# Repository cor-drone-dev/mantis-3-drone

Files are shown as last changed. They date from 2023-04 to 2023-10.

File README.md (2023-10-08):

# mantis-3-drone

Mantis-3 installation instructions

Based on the Chinese guidebook by Clarence Chen

[User Manual](./user_manual.md)

## Installation

1. [Drone Body](./drone_body.md)

2. [Autopilot](./autopilot.md)

3. [Onboard Equipments](./onboard_equipments.md)

4. [Flight Tests](./flight_tests.md)

## Configurations

[MAVROS](./mavros.md)

### Multi-Robot Configurations

[Multi-Drone via MAVROS](./mavros_multi_drones.md)

## Tracking Control

[px4ctrl](./px4_ctrl.md)

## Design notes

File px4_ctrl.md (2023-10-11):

# Tutorial for PX4CTRL

The node name for the PX4 Controller is PX4CTRL.
It takes Odometry and the aircraft's IMU as feedback, receives desired position and attitude control commands, and provides precise control of the aircraft.

## Brief Introduction to the Controller

While the framework of this PX4CTRL controller is similar to the DJI N3 controller, the internal state machine and control algorithms have been completely rewritten to achieve higher stability and control accuracy.
The controller has three modes:

- **Manual Mode**: The terminal prints in green "MANUAL_CTRL(L1)". At this time, the controller does not function, and the flight control is entirely controlled by the remote control.
- **Fixed Point Mode**: The terminal prints in green "AUTO_HOVER(L2)". The controller will take over flight control through code, and the flight control will be in the "OFFBOARD" mode.
  The controller uses odometry feedback for fixed-point control. At this time, if you toggle the direction and throttle joysticks, the aircraft will move slowly, similar to flying in DJI Mavic's fixed-point mode.
  It will not receive the commands you send.
- **Command Control Mode**: The terminal prints in green "CMD_CTRL(L3)". At this time, the controller can execute the flight commands you send to it.
  This mode requires you to be in fixed-point mode, toggle the 6-channel joystick, and then send the control command to start, to ensure a thorough safety check.

### Coordinate System Definition

Odometry's pose is defined as forward x, left y, and up z. The aircraft's head points in the positive direction of the x-axis, and the throttle pull direction is the positive direction of the z-axis. It must be strictly aligned!
The speed definition of Odometry is slightly different from the official ROS. It's essential to note this. The official ROS defines speed under the body system, but most open-source VIOs define speed in the relative world system.
By default, PX4CTRL is also defined in the world system. If the speed you use is defined under the body system, change the `#define VEL_IN_BODY 0` in `input.cpp` to 1.

### Remote Control Channel Settings

PX4CTRL will subscribe `/mavros/rc/in` topic to read the raw RC input.
You need to set and check these values to triggers in QGC:

- Channel 5: Flight mode switch (Recommend: LOW: Manual mode, MID: Position mode, HIGH: Offboard mode)
- Channel 6: Assign a trigger but do not set any function
- Channel 7: Emergency Stop
- Channel 8: Assign a trigger but do not set any function, recommend assigning a joystick that can auto-rebound. (DEPRECATED)

Their corresponding functionalities in `PX4CTRL` are:

- Channel 5: Switch PX4CTRL control (Offboard mode) or the original flight mode of the flight control
- Channel 6: Whether command control is enabled (LOW: Disabled, HIGH: Enabled). When enabled, PX4CTRL will switch to **Command Control Mode** and execute the commands you send.
- Channel 7: Emergency Stop
- Channel 8: One-click restart when the flight control is not unlocked (often used when selecting the ekf2 estimator in the flight control)

### Trajectory Commands

The trajectory command received by PX4CTRL should be a sequence of waypoints in the world coordinate frame.
It is send to the `~cmd` topic as a `quadrotor_msgs/PositionCommand` message.

```
Header header
geometry_msgs/Point position
geometry_msgs/Vector3 velocity
geometry_msgs/Vector3 acceleration
geometry_msgs/Vector3 jerk
float64 yaw
float64 yaw_dot
float64[3] kx
float64[3] kv

uint32 trajectory_id

uint8 TRAJECTORY_STATUS_EMPTY = 0
uint8 TRAJECTORY_STATUS_READY = 1
uint8 TRAJECTORY_STATUS_COMPLETED = 3
uint8 TRAJECTROY_STATUS_ABORT = 4
uint8 TRAJECTORY_STATUS_ILLEGAL_START = 5
uint8 TRAJECTORY_STATUS_ILLEGAL_FINAL = 6
uint8 TRAJECTORY_STATUS_IMPOSSIBLE = 7

# Its ID number will start from 1, allowing you comparing it with 0.
uint8 trajectory_flag
```

### Controller Topics and Services

Check the `px4ctrl_node.cpp` file for the controller's topics and services.
Modify the two topics in `run_ctrl.launch` to the topic names you use. Use `rqt_graph` to check the topic reception to ensure the controller is connected to:
`/mavros/state`
`/mavros/imu/data`
`/mavros/rc/in`
`/mavros/setpoint_raw/attitude`
`/your_odometry`.
And check the frequency of `/mavros/imu/data` and `/your_odometry` is above 100Hz, `/mavros/rc/in` is around 5Hz.

## Usage

The controller runs at the lowest control precision by default. Here, it's as adaptive as possible, so the default parameters are usually sufficient.

Brief usage of the controller is as follows:

1.  Start mavros and your odometry node:

    ```
    roslaunch mavros px4.launch
    roslaunch <your odometry node>
    ```

2.  Start px4ctrl:

        ```
        roslaunch px4ctrl run_ctrl.launch
        ```

3.  Check while the drone is on the ground and not unlocked. In the not unlocked state of the flight controller, toggle the 5th channel switch.
    If the screen prints a message `[px4ctrl] MANUAL_CTRL(L1) --> AUTO_HOVER(L2)` in green, it means the controller check has passed and switched to the hover mode.
    Then toggle the 6th channel joystick. If the screen prints green "[px4ctrl] TRIGGER sent, allow user command.", it means you can switch to command control mode, allowing external control commands to be accessed.
    If errors occur, correct them according to the displayed errors.

4.  Arm the drone on the ground, manually take off to an appropriate height, toggle the 5th channel remote to switch to auto-hover mode, and then toggle the 6th channel remote to switch to control command reception mode.
    Note: Initially, when unfamiliar with the stability of the odometry, it's recommended to check the positioning for drift before switching modes, otherwise the drone may crush as soon as the mode is switched.

5.  When toggling the 6th channel to the **Command Control Mode**, the controller will publish a message to `/traj_start_trigger` topic, which can be used as a trigger to start the planner.
    It also contains the current pose of the drone.

### Troubleshooting

- Although px4ctrl will print detected errors, sometimes errors are emitted by the flight controller and cannot be detected by px4ctrl, manifesting as inability to take off, no response when switching to hover, etc.
  These in-flight-controller errors will be printed on the QGC ground station.
- If mavros reports a serial port error, check if the serial port has not been granted 777 permissions (sudo chmod 777 /dev/<serial port name>).
  If the serial port opens successfully but there's no response, check if the cable is connected correctly or if the MAV_1_CONFIG parameter of the flight controller is set incorrectly.
- If other errors are reported, check if you missed installing the geographiclib.
- When using ekf2 as the flight controller's state estimate, it's common to encounter the inability to unlock after landing, reporting attitude estimation errors.
  At this time, toggle the remote's 8th channel, and the flight controller will restart, resolving the error.
- If the drone continuously flies up or down after switching to hover mode, excluding positioning drift, it's mostly because the throttle stick hasn't returned to the center.
  Because in hover mode, remote control is allowed. Solution 1: Manually return the throttle stick to the center, as there is a dead zone set near the center; Solution 2: Set max_manual_vel in the config to 0, i.e., disable the remote control function in hover mode.
- If the drone's position fluctuates up and down after switching to hover mode, excluding positioning drift, it's mostly due to the throttle model estimation, which is caused by excessive IMU vibration during flight, leading to inaccurate throttle model feedback.
  Poorly damped IMUs can have accelerometer vibrations between ±5~10m/s^2, while well-damped IMUs (like DJI N3, Lei Xun Nora, X7, etc.) usually don't exceed ±0.3m/s^2.
  You can record an imu bag file during flight to check. Although you can alleviate the issue by adjusting controller parameters, it's still recommended to have proper damping for the entire drone.
  Therefore, the parameter "rho2" is set to be unchangeable. To dampen, buy dedicated IMU sponge dampers and stick them to the four corners of the flight controller. The expected vibration should be less than 2m/s^2.
- Continuing from the previous issue, if you really can't reduce the vibration, you can choose
  - 1: Change the noisy_imu parameter in the config file to true, which will change the acceleration feedback to speed feedback but will significantly sacrifice dynamic performance;
  - 2: If you don't mind steady-state control errors, you can directly comment this parts out from the code

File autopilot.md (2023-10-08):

# Autopilot

## 1. PX4 Autopilot

### 1.1 PX4 Autopilot Firmware Flashing

Disconnect the battery, insert the TF card into the flight controller, and then use a USB cable to flash the firmware.

If you are using Holybro KakuteH7v2, you need to flash the PX4 firmware following this [link](https://docs.px4.io/main/en/advanced_config/bootloader_update_from_betaflight.html#dfu-util).
First you need to install the firmware from the official [repo](https://github.com/PX4/PX4-Autopilot), next compile it with `make holybro_kakuteh7v2_bootloader`, then replace `build/<target>/<target>.bin` to the path of your compiled binary file.

### 1.2 Autopilot Parameter Configuration

Connect the flight controller to the computer with a USB cable and open the QGC software, and wait for the flight controller to connect. Refer to the video in <https://docs.px4.io/main/en/config/>, or the graphic tutorial on that webpage, to set up Airframe, calibrate Gyroscope, accelerometer, and Level Horizon, configure Radio channels, Flight Modes, and Battery step by step. Choose the **Generic X Type** quadcopter for Airframe, and the specific type can be DJI F330. Different types correspond to different preset parameters. Later, the parameters used by this aircraft will be reloaded.

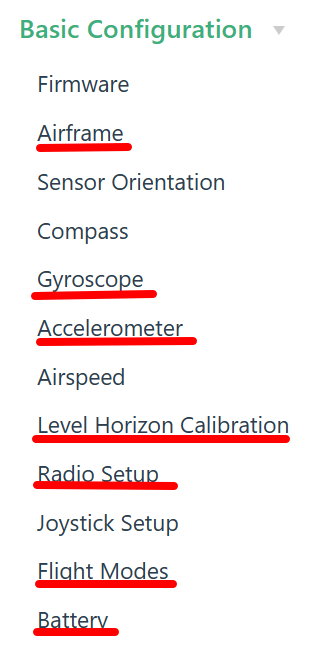
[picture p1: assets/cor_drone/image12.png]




\*\*Important: Next, you need to set the two parameters shown in the following figure in the _Parameters_ option (Parameters) of QGC to ensure the safe takeoff and flight of the drone\*\*

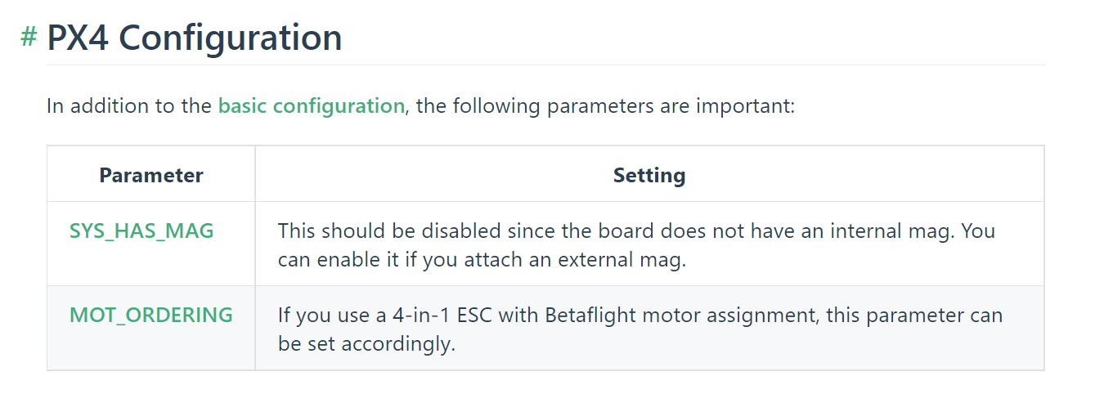
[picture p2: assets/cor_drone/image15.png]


### 1.3 Test Motor Rotation Direction

The normal direction of motor rotation should be as shown in the following figure. The red arrow points to the direction of the aircraft's head, which is the direction indicated by the triangle-shaped marking on the flight controller. When the four motors are placed **facing downwards** (as shown in the figure), the direction of rotation as viewed from **above** should be as indicated by the arrow in the figure. To test the motor rotation, you need to power on the battery (do not install the propellers!) and then you can use one of the following two methods to check the motor rotation.

1. Method 1: **Use QGC**
   - Please refer to <https://docs.qgroundcontrol.com/master/en/SetupView/Motors.html> for the new method provided by the official. _It looks very convenient but we haven't tried it yet._
2. Method 2: **Use the remote controller**
   - First unlock the remote controller joystick with the eight shape, and then gently push the throttle to make the motor rotate. In order to prevent the motor from flying around, you can find something to support the middle board, and then use your hand to hold the motor wire to make the motor hang in the air. Check the direction of all the motors and record whether the direction of the motors is correct. If the direction is wrong, reverse two motor wires and re-solder them. Then test the direction of the motor again to ensure that the direction is correct.

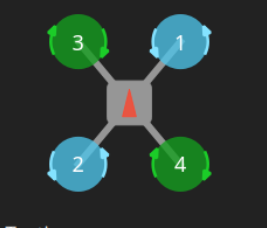
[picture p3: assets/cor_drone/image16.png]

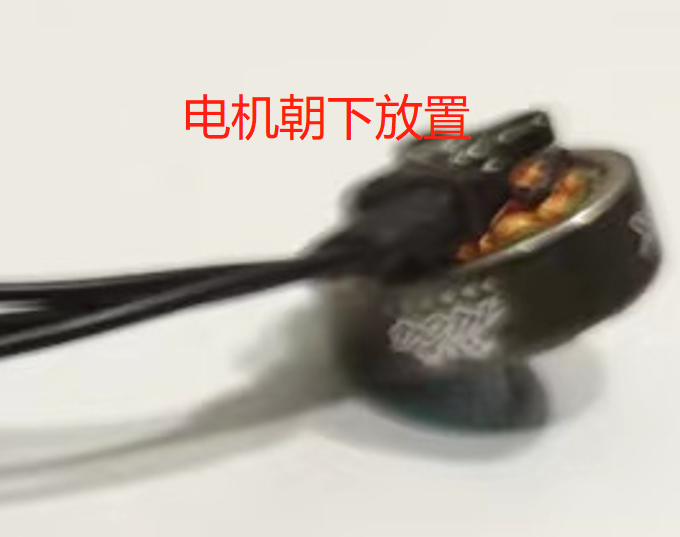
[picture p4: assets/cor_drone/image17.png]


## 2. Ardupilot Flight Controller (APM)

There are two reasons for using APM firmware: (1) the Kakute H7V2 cannot be flashed with PX4 firmware (Although you can flash the firmware, you cannot arm the drone); (2) APM firmware supports bi-directional Dshot, which can increase the upper limit of motor speed feedback frequency, and is suitable for use scenarios that require motor speed feedback (although it seems that the PX4 is going to support bi-directional Dshot recently). In short, if you are using Kakute H7V2 or Kakute Mini, or need high frequency motor speed feedback, APM firmware is recommended.

### 2.1 Firmware Flashing

Here is an example of firmware flashing for Kakute series flight control. First, use the Stm32CubeProgrammer software to flash the Bootloader.

1. The Bootloader can be downloaded from https://firmware.ardupilot.org/Copter/stable-4.3.5/. Note that the corresponding version of Kakute H7V1 is KakuteH7-bdshot; the corresponding version of Kakute H7V2 is KakuteH7v2; the corresponding version of Kakute H7Mini is KakuteH7Mini-Nand.
2. Enter the corresponding directory of the above URL, download the arducopter_with_bl. hex file, press and hold Reset to enter DFU mode, and finally use the `Stm32CubeProgrammer` software to flash it.
3. After the Bootloader and the flight control firmware have been successfully flashed, open the QGC or Mission Planner and other ground stations can already be successfully connected with the flight control.
4. If you need to use your own modified flight control, you do not need to flash the bootloader again, you may flash compiled firmware generated apj file directly in the QGC.

### 2.2 Firmware parameters debugging

After the successful flashing of the firmware, in order to debug the aircraft, to achieve hand control performance, while being able to correctly communicate with the upper computer, you need to make the corresponding firmware parameters adjustment.
Specific reference to the document here: https://charmyoung.notion.site/APM-697b52589579465991e380da97c71c61#f20fdc5555d44b1fba0b05fae0ea1c65

Among them, the most noteworthy options are: (1) GUID_OPTIONS needs to be set to 9; (2) the upper, middle and lower modes of Channel5 of the remote control are set to Stabilize, Stabilize, and Guided_Nogps; (3) MOT_THST_EXPO is recommended to be set to 0, which means the flight control is completely using linear throttle model, so that the hover_percentage in px4_controller can be set directly to the hover throttle value.

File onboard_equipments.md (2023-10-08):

# Onboard Equipments

In this tutorial, the onboard computer used is the NVIDIA Jetson Xavier NX combined with the Seeedstudio A203v2 carrier board. The onboard computer runs JetPack 5.0.2, which is a Ubuntu 20.04 system. The camera we use is a Realsense D455 without a housing module, that is, a customed module of Realsense D450 depth camera and Realsense D4 V3 vision processor board.

## 1.1 Camera Installation

The camera comes with the accessories shown in the figure below, from left to right, they are the computing board, connection cable, camera sticker, camera module. We also need to install the 3D-printed Realsense mounting base.

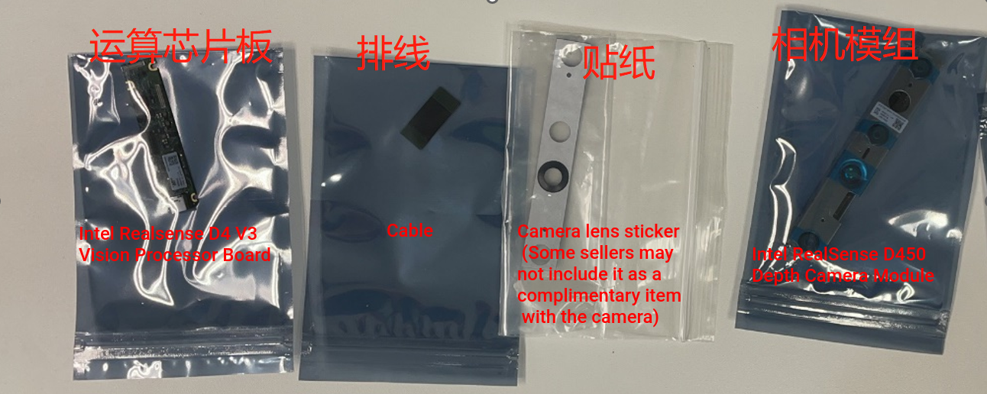
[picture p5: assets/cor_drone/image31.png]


The installation process is very simple. First, stick the camera sticker on the side of the camera module with the lens. Then, install the camera module on the mounting base with the protruding screw holes on the ribbed side. Next, install the computing board on the back of the mounting base according to the screw holes, noting that there are two sets of holes on the back of the mounting base for installing the computing board. When using a straight-line cable (such as the one shown in the figure), the computing board is installed in the middle position. When using a Z-shaped cable, the computing board is installed in the edge position. The installation uses self-tapping screws of M2x8mm or M2x6mm.

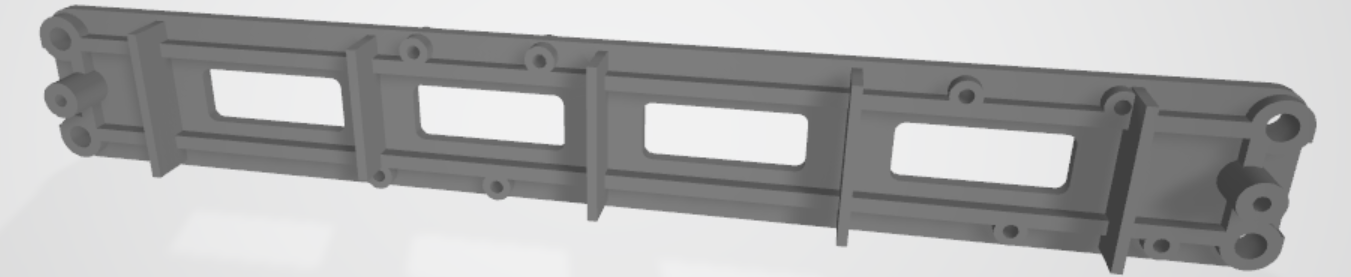
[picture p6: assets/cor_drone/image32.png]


After installation, connect the ribbon cable. The final result with a Z-shaped ribbon cable is shown below. When using a straight ribbon cable, the result will be similar, with the computing board located closer to the center.

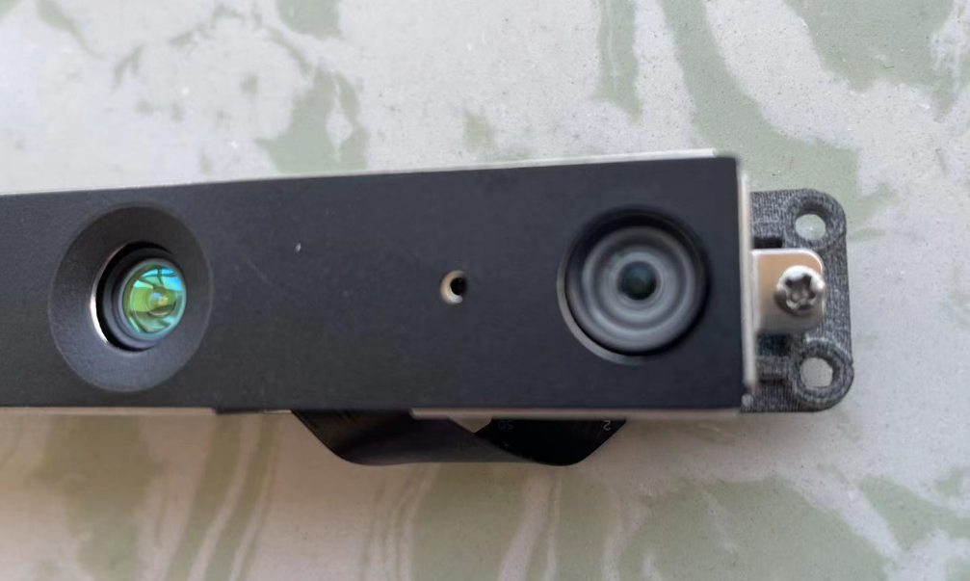
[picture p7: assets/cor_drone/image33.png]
 
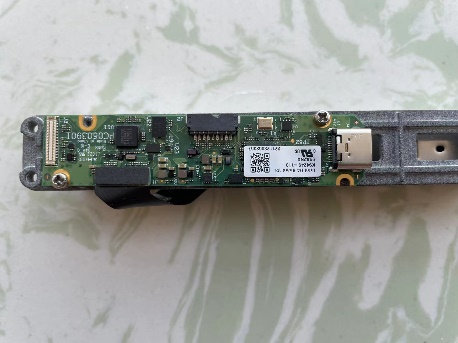
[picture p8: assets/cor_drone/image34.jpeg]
 
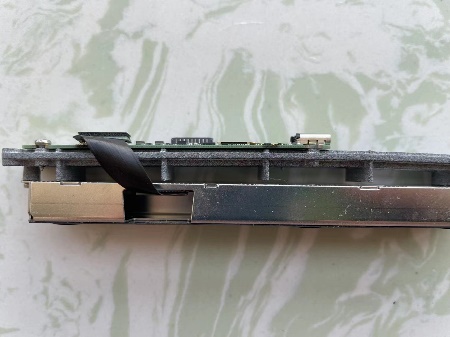
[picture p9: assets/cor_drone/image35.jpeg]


## 1.2 Installation of Onboard Computer

### 1.2.1 Installing a Cooling Module on NX Board

First, we should take Jetson Xavier NX board from the package carefully.
Before mounting it on the carrier board, we should install a cooling fan onto the board.
Use the screws and thermal metal plate come with the cooling module to fix it with the NX board.
Remember to connect the power cable of the cooling module with the carrier board at the end of onboard computer installtion.

### 1.2.2 Installing Wi-Fi Module on the Carrier Board

Before installing the NX board on the carrier board, we should install the Wi-Fi module on the carrier board.
The Wi-Fi module we use is Intel AX210, which has a M.2 interface and supports 5GHz Wi-Fi.
Remember to order the Wi-Fi module with the antenna.
Next, insert it into the M.2 slot located on the underside of the carrier board, and secure it with a M2x4mm screw (You can use the one with the carrier board.)

### 1.2.3 Installing NX Boards on the Carrier Board

Then, we should install all the circuits on to the carrier board.
Please note that the underside of the carrier board features a 40-pin slot specifically designed for the Jetson NX.
The next step is to carefully insert the Jetson NX module into this slot at an angle of 30 to 40 degrees.
It will be fixed automatically.
Use the same M2x4mm screws to secure the NX module.
Finally, insert the TF card into the onboard computer to use as a hard drive.
If you choose to use NVME SSD, you may insert it into the M.2 SSD slot and fix it with screws.

Then, insert the onboard computer into the mounting bracket from the back upper side, and use M2.6x8 self-tapping screws to fix the onboard computer. Note that there are two screws in the front and two in the back that need to be installed. The installation is shown in the figure below.

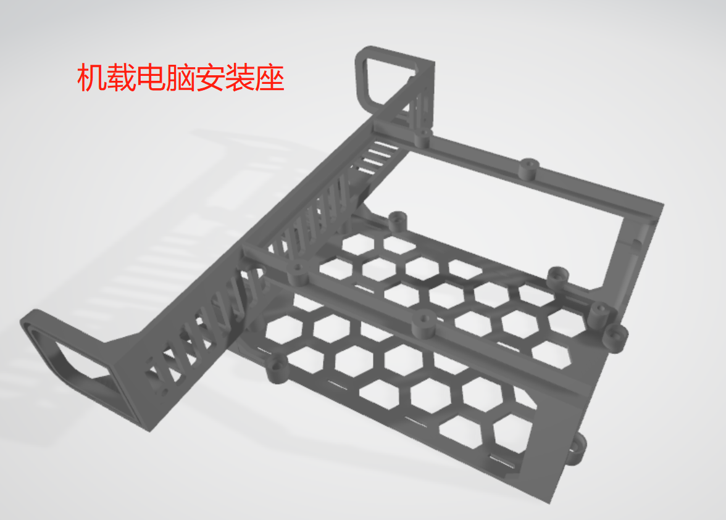
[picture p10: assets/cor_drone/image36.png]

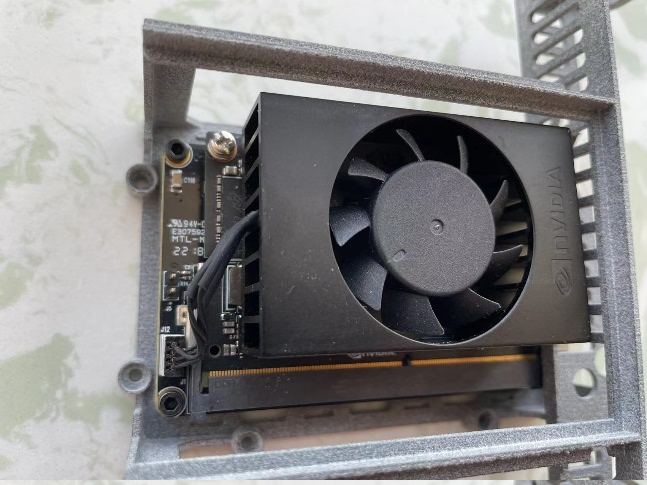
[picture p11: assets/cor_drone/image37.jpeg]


Finally, fix the installed camera module in front of the onboard computer installation seat using M2.6x8 self-tapping screws, with the camera cable facing downwards. When installing, be careful not to pinch the cable. **A thin rubber sleeve or rubber pad can be placed on the screw between the camera module and the onboard computer installation seat for shock absorption.** The installation is shown in the following figure.

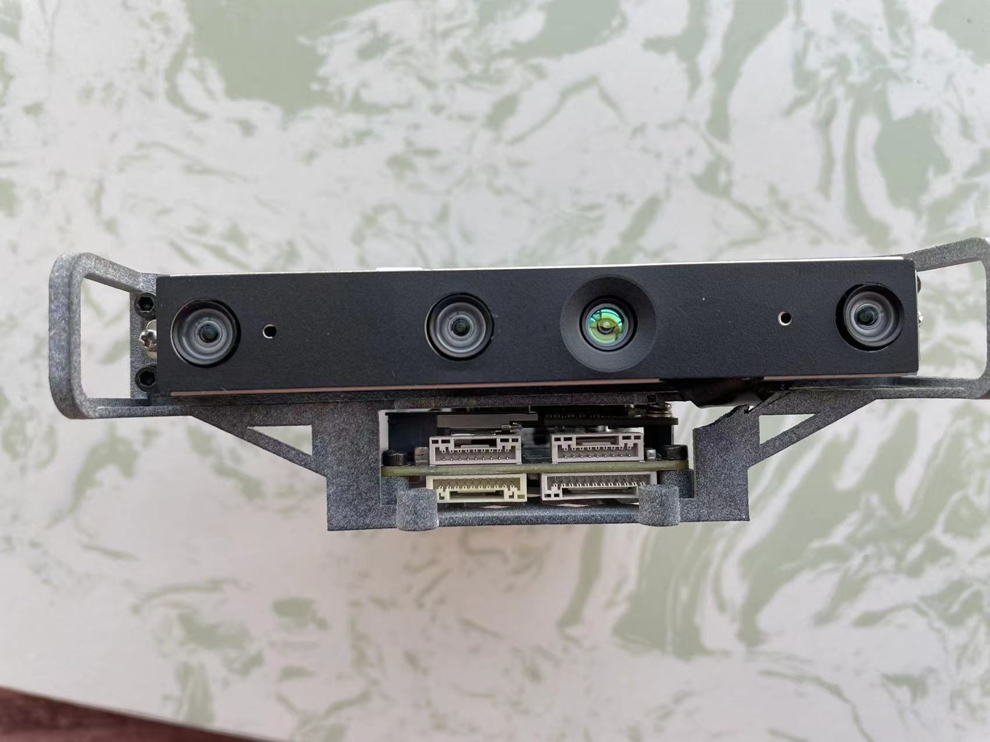
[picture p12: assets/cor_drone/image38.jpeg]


Connect the keyboard, mouse, and monitor to the onboard computer, and power it using the onboard computer's built-in voltage regulator. Then, turn on the computer.
Please refer to the official ROS website and Realsense website for installation instructions.
(<https://dev.intelrealsense.com/docs/nvidia-jetson-tx2-installation>)
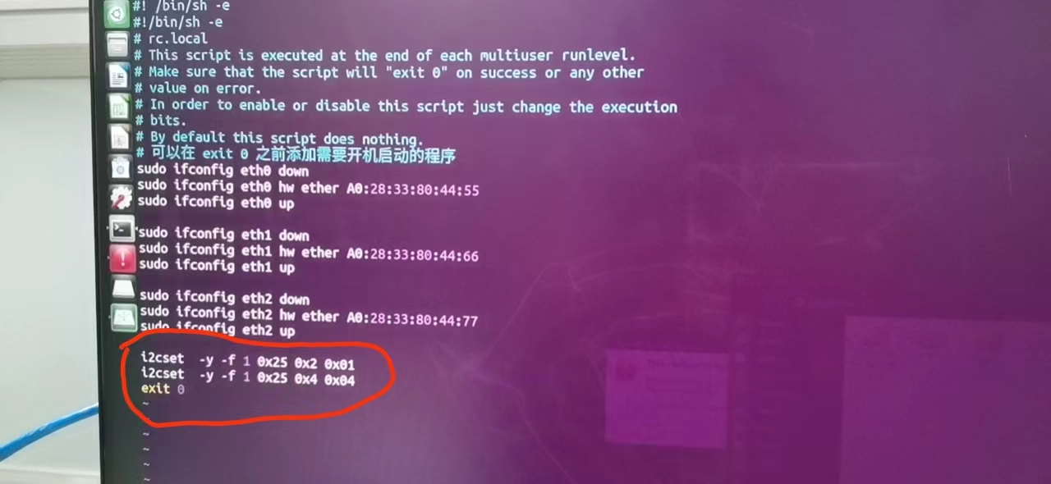
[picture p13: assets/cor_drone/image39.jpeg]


### 1.2.4 Flashing JetPack OS to the Boards

You may follow the manual [here](https://wiki.seeedstudio.com/reComputer_A203_Flash_System/) to flash the system via NVIDIA SDK Manager with GUI.
If you're using a Linux desktop, I would recommend to [flash JetPack via command line](https://wiki.seeedstudio.com/reComputer_A203_Flash_System/#flashing-jetpack-os-via-command-line).
Remember if your Jetson Xavier NX is a 16GB version, you should be careful at the step 6 or step 4: _Unzip the Driver in the system folder_.
At this step you replace the `.dtb` files which describes ports on the carrier board.
Since the product number of Jetson Xavier NX 16GB version is `p3668-0003`, you need to make sure `.dtb` files with the same name is replaced.
Otherwise, the TF card may not be detected in JetPack OS.
I would recommend to rename `tegra194-p3668-0001-p3509-0000.dtb` file to `tegra194-p3668-0003-p3509-0000.dtb`.

### 1.2.5 How to copy system to TF/SD card?

1. Plug in the source TF/SD card `/sdb1` and destination card `/sdc1`. You may use `lsblk` to check the mounting position
2. There are two approaches to copy SD card

   - **Clone**: You can clone all blocks on the source card by using `dd` command:

     ```
      sudo dd if=/dev/sdb1 of=/dev/sdc1 status=progress

     ```

   - **Copy**: If the storage size of source card is different from that of destination card, you may copy the system file using `rsync` command:

     ```
     sudo rsync -axHAWX --numeric-ids --info=progress2 --exclude={"/dev/","/proc/","/sys/","/tmp/","/run/","/mnt/","/media/*","/lost+found"} /dev/sdb1/ /dev/sdc1
     ```

### 1.2.6 How to copy NVME SSD?

To copy your Ubuntu system from `nvme0n1p1` to a new SSD, you generally need to follow these steps:

1. **Backup Important Data**: Always create a backup of your important data to an external drive or a cloud storage solution before proceeding.

2. **Boot from a Live USB/CD**: Before you can copy your system, boot your computer from a live Ubuntu USB or CD. This ensures that the partitions are not being used while we're copying them.

3. **Identify Drives**: Once you're in the live environment, open a terminal and type:

```bash
sudo fdisk -l
```

This will list all the drives and their partitions. Identify the source (`nvme0n1p1` in your case) and the destination (your new SSD, e.g., `sda` or similar).

4. **Use `dd` to Clone**: Once you've identified the correct drives, use the `dd` command to copy your system over:

```bash
sudo dd if=/dev/nvme0n1p1 of=/dev/sdX bs=64K conv=noerror,sync status=progress
```

Replace `/dev/sdX` with the appropriate identifier for your new SSD.

5. **Resize the Filesystem** (if needed): If your new SSD is larger than the original `nvme0n1p1`, you'll have some unallocated space. To use this space, you need to resize the filesystem and possibly the partition.

   - For ext4 filesystem:

   ```bash
   sudo resize2fs /dev/sdX1
   ```

6. **Update the GRUB bootloader**: The boot sector might need to be updated:

```bash
sudo grub-install /dev/sdX
sudo update-grub
```

Replace `/dev/sdX` with the identifier for your new SSD.

7. **Update `/etc/fstab`**: The UUID of your new SSD will be different. Mount your new SSD partition and update the UUID in `/etc/fstab`:

```bash
sudo blkid /dev/sdX1
```

This will give you the UUID. Now, mount the partition:

```bash
sudo mount /dev/sdX1 /mnt
sudo nano /mnt/etc/fstab
```

Find the line with `/` (root filesystem) and replace the UUID with the one from the `blkid` command. Save and exit.

8. **Reboot**: Once everything is done, reboot your computer. Ensure your BIOS/UEFI settings are set to boot from the new SSD.

Note: The `dd` command is very powerful and also very dangerous. Make sure you've correctly identified source and destination to avoid data loss. If you're unsure about any steps, seek assistance from someone familiar with Linux disk operations.

### 1.2.7 How to copy JetPack NVME SSD and boot from EMMC?

After I copied SSD, I discovered that the system cannot boot from it.
Therefore I choose to boot from EMMC selecting NVME as the boot device.

1. launch from EMMC, and modify `/boot/extlinux/extlinux.conf`. You might need to back up before save.
2. modify `root=/dev/mmcblk0p1` to `root=/dev/nvme0n1`
3. modify the label of boot options: `LABEL primary` to `LABEL nvme`, `MENU LABEL primary kernel` to `MENU LABEL primary NVME`
4. boot from EMMC

### 1.2.8 Network Configuration

If the onboard computer cannot connect to the Wi-Fi network, you may need to configure the network manually.
You need to download the corresponding firmware from this [link](https://www.intel.com/content/www/us/en/support/articles/000005511/wireless.html)
and copy the `.ucode` file to `/lib/firmware/` directory.
Then, you may use the following command to configure the network:

```bash
tar xzf iwlwifi-cc-a0-*.ucode.tar.gz   # unzip the firmware
```

Next, copy the `.ucode` file to `/lib/firmware/` directory.

```bash
sudo cp iwlwifi-cc-a0-*.ucode /lib/firmware/
```

## 1.3 Connection between Onboard Computer and Camera

The onboard computer and Realsense camera are connected via a USB 3.0/3.1/3.2 cable.
The RealSense has a Type-C interface, and the carrier board has 2 USB 3.0 interface, so you need to find a USB 3.0 Type-C cable.
After connecting the cable, you can use the `lsusb` command to check if the camera is connected.
Then, you may use the `realsense-viewer` command to check if the camera is working properly.
Please take note that the RealSense depth camera requires a USB 3.0 connection to function properly.
Using a lower bandwidth connection may result in insufficient data transmission capabilities.
If the connection is USB 2.0/2.1, it may be due to the USB Hub or the USB cable used is not 3.0.

Possible connection problems are:

1. _SKU Invalid_ when plugin the realsense camera

   Solution: According to Intel forum, directly update the firmware for D4 V3 board without D450 camera module.

2. When launch the realsense node, continuously receiving error: `control_transfer returned error, index: 768`

   Solution: `sudo apt purge ros-noetic-librealsense2`

3. `lsusb` or `rs-capture` takes too long time to response

   Solution: The only reason is the HSF100 cable is not well connected, chech the hardware connection and pins.

4. `realsense-viewer` displays `USB 2.0 (High-speed)` in the upper left corner

   Solution: The USB 3.0 cable is not connected properly, or the USB 3.0 cable is damaged.

## 1.4 Mounting Onboard Computer on Drone

During flight, the onboard computer needs to be powered by a separate power line from the battery or ESC soldering pad.
The mounting bracket for the onboard computer has four installation holes.
Align the bracket with the corresponding holes on
the top of the aircraft, then use M2.6x8 self-tapping screws to mount it to the aircraft.

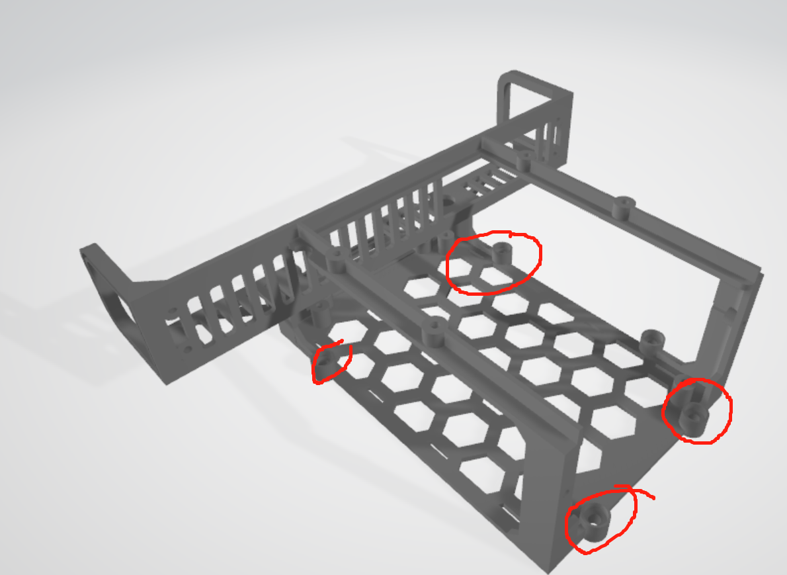
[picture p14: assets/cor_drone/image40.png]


The drone after the installation is completed is as follows.

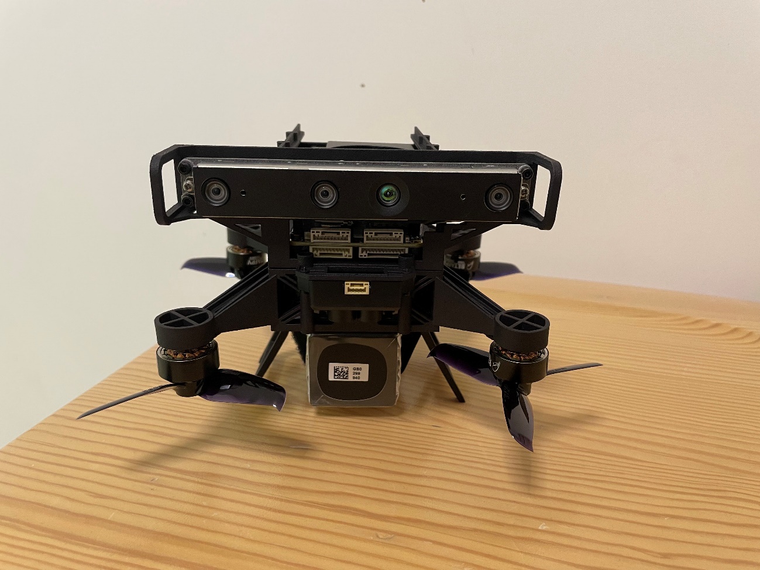
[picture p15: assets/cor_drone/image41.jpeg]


## 1.5 Connection Between Flight Controller and Onboard Computer

The onboard computer communicates with the flight controller by connecting a USB to TTL module to the USB port.
Note that the maximum baud rate supported by the onboard computer's built-in serial port is not high enough (generally up to 115200), so the USB to TTL module is necessary. It is recommended to use a CP2102 serial port module, or other serial port modules such as PL2303 or CH340 can also be used. For the onboard computer used in this manual, it has only one USB Type-C interface, so a USB hub is needed to connect both the USB to TTL and the Realsense camera.

Next, we will introduce the software configuration to make the onboard computer and the flight controller communicate properly.
On the flight controller side, we have completed the communication settings with the onboard computer (i.e. MAV_2, Onboard).
On the onboard computer side, we need to fix the device port number of the USB to TTL and start MAVROS to achieve communication, as follows:

1. Bind the device port number of the USB to TTL, which can refer to the method in <https://unix.stackexchange.com/questions/66901/how-to-bind-usb-device-under-a-static-name> and name the USB to TTL device with a name you want, such as PX4.
2. On the onboard computer, we need to install ROS and use the commands `sudo apt install ros-xxx-mavlink` and `sudo apt install ros-xxx-mavros` to install MAVROS. Use the command `roscd mavros` to open the `/opt/ros/xxx/share` folder where MAVROS is located. Then open the `Launch` folder where there is a launch file to start MAVROS, for example `px4.launch` for the PX4 firmware. We need to modify this file, but to avoid damaging the original file with incorrect modifications, we can copy and paste it to create a new file named `px4_companion.launch` using the command `sudo cp px4.launch px4_companion.launch`. Then, modify the `px4_companion.launch` file with the following changes:
   - Change the device name to `/dev/` followed by the name you gave to the USB to TTL device, for example `/dev/PX4`. If you forgot the name, you can use the command `ls /dev` to check.
   - Change the baud rate to 921600.
3. To check if the communication between the onboard computer and the flight controller is working properly. Here's a summary of the steps:
   - Start the MAVROS launch file by running `roslaunch mavros px4_companion.launch` on the onboard computer.
   - Check if the receive and transmit lights on the USB to TTL module are on or flashing, which indicates that communication is working properly.
   - Run `rostopic echo /mavros/state` command to check if the connection is normal.
   - If the connection is not normal, check if the hardware connection described in section 3.1 is correct and if the flight controller settings described in section 1.11 are correct.
     - If there is a serial port permission problem, you can use the following command to solve it once and for all.
       ```shell
       sudo usermod -a -G dialout $USER
       sudo apt-get remove modemmanager -y
       ```
       `After` logging out the system and logging in again, the permission manager of the onboard computer will be uninstalled to avoid the serial port The problem of no permission to open the serial port will be avoided.

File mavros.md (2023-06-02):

# Controlling Drone via MAVROS

## Setting ROS message frequency

## Getting odometry from Opti-track

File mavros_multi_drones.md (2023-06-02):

# Controlling Multiple Drones via MAVROS

In this file you will learn how to setup MAVROS for multiple drones on the same ROS network.

For MAVROS setting, you can refer to [Controlling Drone via MAVROS](./mavros.md)

## Connecting to QGroundControl

First, we need to allocate a unique ID to each flight controller.
Connect to drone 1 via cable connection and go to `Vehicle Setup -> Parameters` set the parameter `MAV_SYS_ID` to 1.
Then, switch to drone 2 and set the same parameter to 2.

Go to `Application Settings -> General` and disable **AutoConnect**

Next, go to `Application Settings -> Comm Links` add connection manually.
You can click `Add` button on the bottom and set the name of the connection. Then click `Type`, set UDP connection, change the UDP address to the `gcs_url` address above.
On this page, you have the option to connect or disconnect individual drones.

Finally, save the settings and add the connection settings for the 2nd, 3rd drone.

After setting up all the connections, launch the mavros node on each drone and click `connect` at QGroundControl to connect them one by one.

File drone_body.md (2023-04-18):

# Installation of Drone Body

## 1.1 Motor ESC

Take out the Electronic speed control(ESC) and four motors as shown in the figure below. The ESC may have been purchased together with the flight controller as a flight tower, and needs to be removed first for convenient soldering of the circuit. The white interface on the top of the ESC is for connecting the data cable of the flight controller, and the metal solder pads below will be soldered with power supply connectors. There are a total of 3x4 solder pads on the left and right sides, corresponding to four three-phase brushless motors. Numbers 1, 2, and 3 in the figure correspond to the three wires of a motor.

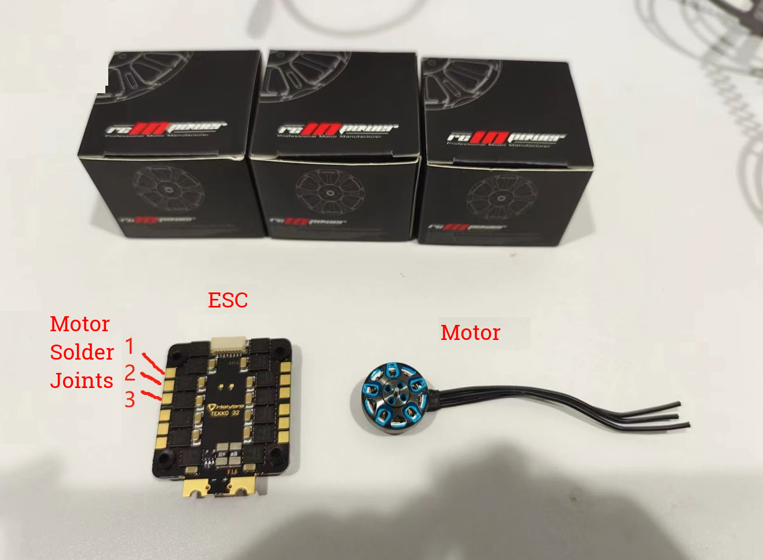
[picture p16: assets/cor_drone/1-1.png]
ESC and motors


## 1.2 Welding the Motor

Shorten or lengthen the motor wires to about 75mm. For Betaflight series motors, the manufacturer shortens the wires to save money, so you need to extend the wires yourself. Pay attention to putting heat shrink tubing on the soldering points to prevent short circuits. The welding sequence can be welded according to the line sequence diagram below. The motor is placed axially upwards, marked from top to bottom as lines 1, 2, and 3, corresponding to the 1st, 2nd, and 3rd positions on the solder pads of the ESC. For Betaflight 1506 motors or Zhiying Power 1404 motors, as well as Holybro TEKKO 32 ESC, there is no need to adjust the line sequence after welding according to the order in the figure. (For three-phase brushless motors, there is no positive or negative polarity. If any two wires are reversed, the direction of the motor rotation will be reversed)

Tips: When welding, you can evenly apply solder to both ends of the wire or solder pad first, then place them together and use a soldering iron to heat the solder that has been applied to make them stick together. This method is more efficient and has a higher success rate. At the same time, pay attention not to heat the soldering pad for a long time. After the solder melts and sticks together, you can remove the soldering iron. Otherwise, the high temperature of the ESC may cause damage to electronic components. Beginners can pull the wire after welding to see if it is firmly welded.

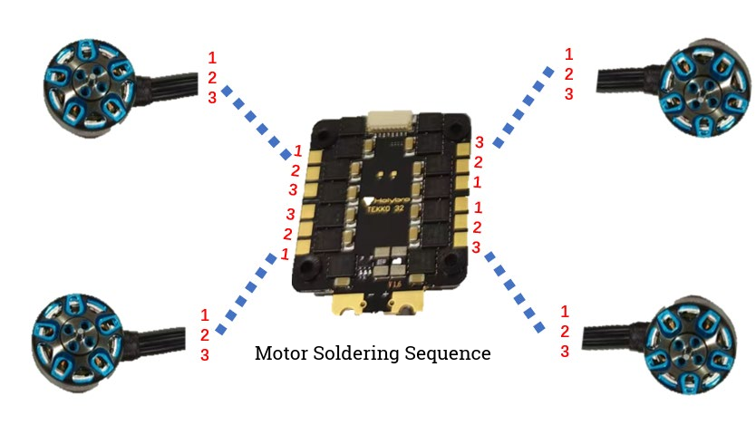
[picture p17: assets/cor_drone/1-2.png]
<figcaption>Motor wire sequence diagram</figcaption>

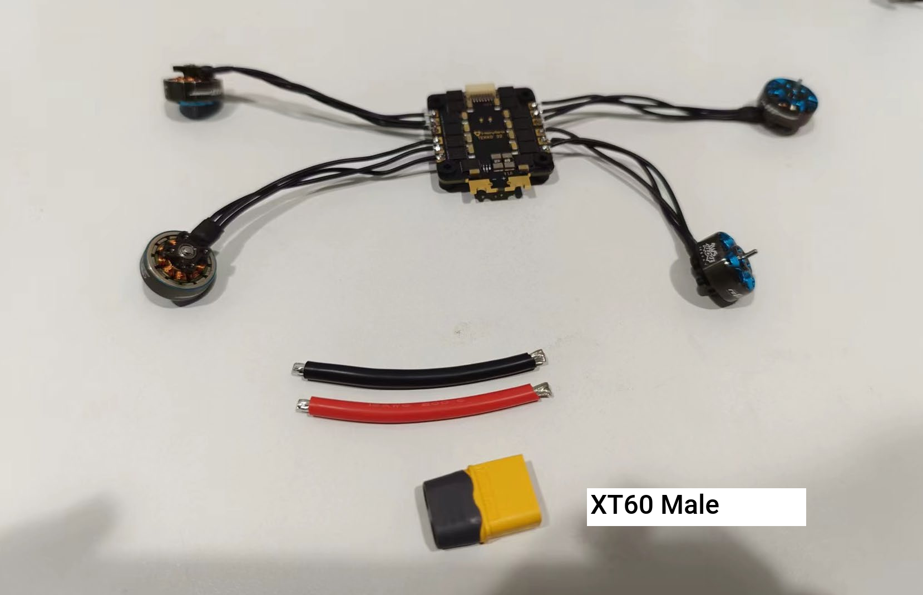
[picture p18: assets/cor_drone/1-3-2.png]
<figcaption>Motor wire sequence diagram</figcaption>

## 1.3 Wiring the Power Supply

Solder the XT60 connector and the positive and negative wires to the soldering pads located below the ESC. If the XT60 connector and wires are sold together (as shown in the small image below), you only need to solder them to the ESC. If the wires are too long, you can cut them to about 5cm in length before soldering.
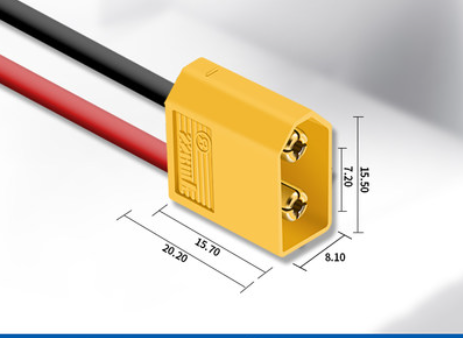
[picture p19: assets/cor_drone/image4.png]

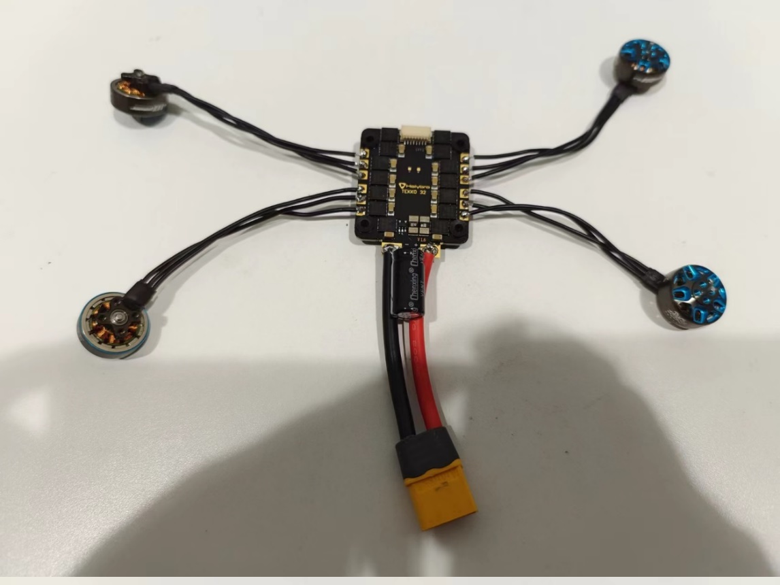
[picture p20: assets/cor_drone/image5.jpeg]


If the ESC comes with a capacitor or you have a larger capacitor with a rated voltage greater than 20V, you can solder it to the solder pad in parallel with the power supply wires by shortening the positive and negative terminals (the negative terminal is usually marked with a "-" sign), as shown in the figure below after soldering is completed:

> Tips: After soldering is completed, it is recommended to use a multimeter to test whether the positive and negative terminals are short-circuited (there should generally be a resistance value of several hundred ohms or more, and should not be directly short-circuited), to ensure that the soldering is correct. If a flight computer is to be installed later, two wires need to be led out from the power supply solder pads and connected to an XT30 connector or other plug for supplying power to the flight computer in the future.

## 1.4 Connecting the flight controller

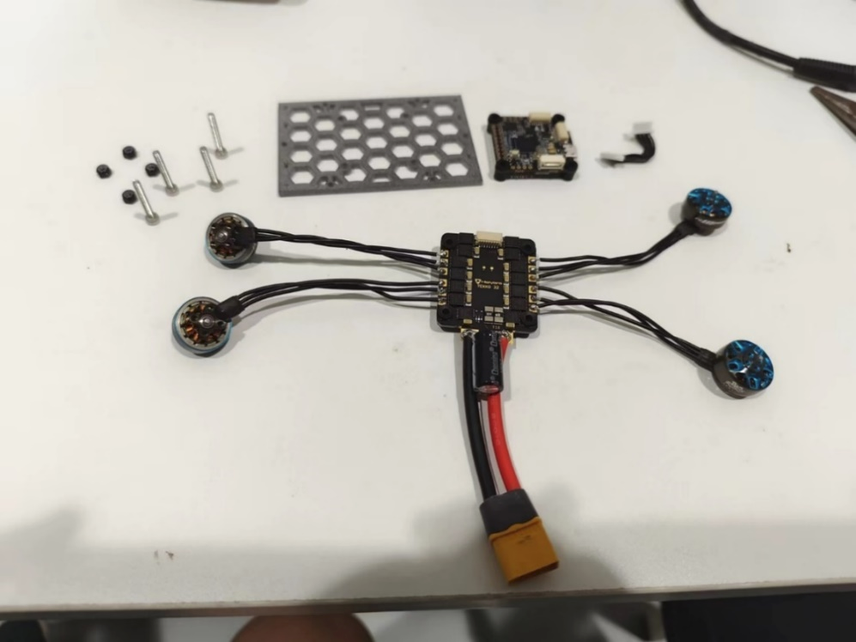
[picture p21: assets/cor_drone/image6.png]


Remove the flight controller, long M3 screws and anti-loose nuts (which should come with the flight controller and ESC kit), and then use screws to install the flight controller, ESC and the 3D-printed intermediate plate together. Put shock-absorbing rubber sleeves on the screws between the flight controller and ESC, and between the ESC and the 3D-printed board. Pay attention to the direction indicated by the triangular silk screen on the flight controller, which is the front direction and should be consistent with the front direction of the ESC (the direction with the white connector). The 3D-printed intermediate plate has no front or back direction.

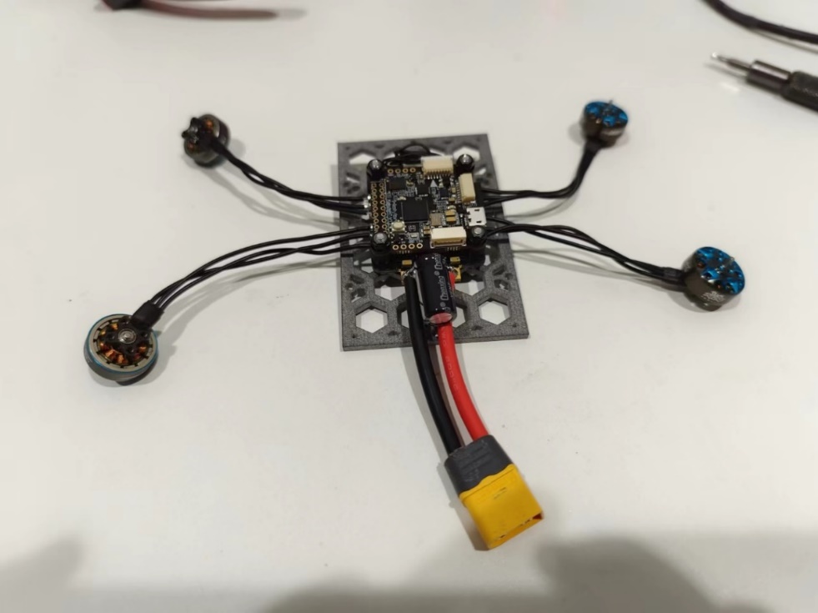
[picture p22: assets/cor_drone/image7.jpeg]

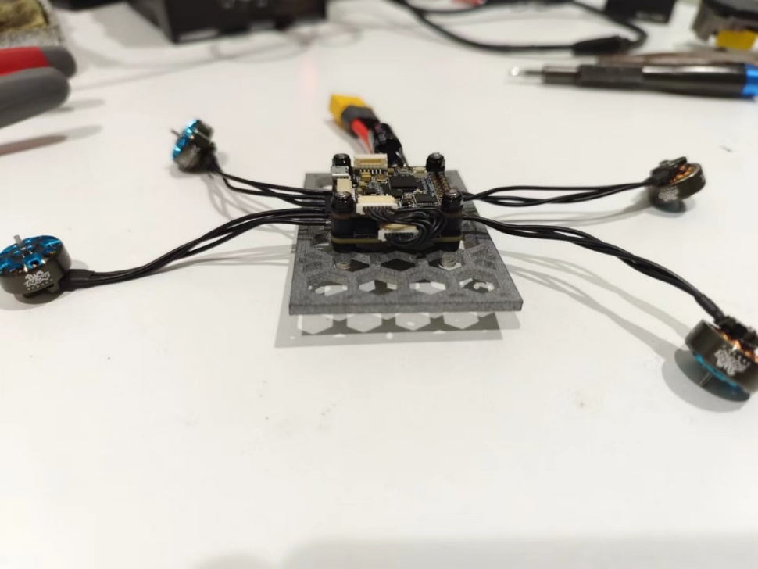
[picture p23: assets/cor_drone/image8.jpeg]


After installing the screws, connect the signal ribbon cable between the flight controller and ESC, with the connector towards the front direction. The top view and front view of the completed connection are shown below:

## 1.5 Connecting the Receiver

The receiver is mainly responsible for receiving signals from the remote control to control the drone. The signal ports of the receiver (Output1, SBUS) are connected to R6 of the flight controller, which requires a power supply of 5V. The connection steps are as follows: locate the 6-pin plug on the flight controller and connect it to the interface shown in the red box in the figure below. The wiring sequence is shown in the lower right corner, so the left two wires of the 6-pin plug (R6, G) need to be soldered respectively to the signal port (Output1, SBUS) and GND of the receiver. **The R1, T1, and G wires on the right side of the 6-pin plug are reserved and will be used for communication with the onboard computer later.** The wire corresponding to 9V on the far right is not used and can be cut off. In addition, the receiver needs a power supply of 5V, which can be connected to the corresponding 5V port of the receiver with the left 5V port of the plug that has been cut off or other wires.

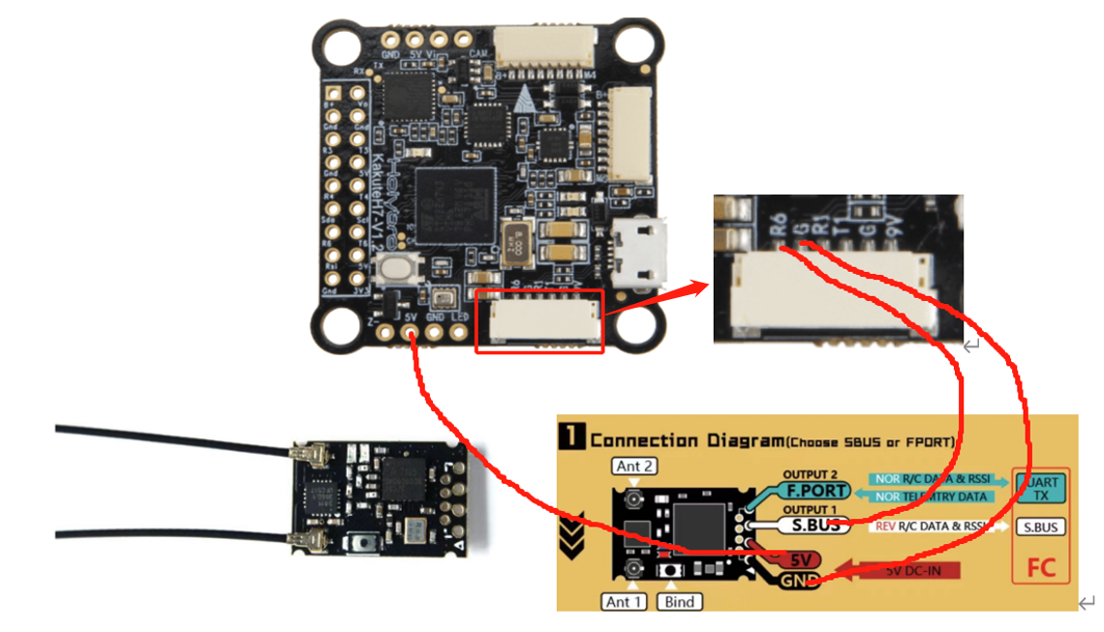
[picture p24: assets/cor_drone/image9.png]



After the connection is completed, it should look like the figure below. Use foam double-sided tape to stick the receiver to the lower right corner of the 3D printed board, mainly to avoid blocking the screw holes.

## 1.6 Connecting the TTL to USB module

In step 1.5, we have reserved the T1, R1, and G interfaces on the flight controller, which are the send, receive, and ground interfaces. Here, T1, R1, and G should be connected to RX, TX, and G of the USB to TTL module, respectively, that is, receive to send, and send to receive. The power supply line does not need to be connected, and the USB to TTL module will be powered by the USB port of the onboard computer (HUB). The connection diagram is as follows:



## 1.6 Remote Control Pairing

Connect the XT60 plug to the 4S lithium battery purchased for power supply. After powering on, the receiver light is on and flashing slowly, indicating that it is not paired. Press and hold the button in the circle in the figure below for 2 seconds, and the receiver indicator light will flash quickly, entering pairing mode. Turn on the Futaba remote control, and the receiver light will stay on when the pairing is successful. When the remote control is turned on, it will automatically search for available receivers. Therefore, when the receiver is in pairing mode, simply turn on the remote control to pair.



## 1.10 Installing Wireless Data Transmission

Solder the TX, RX, 5V, and GND of the wireless data transmission module to the T4, R4, 5V, and GND of the flight controller, respectively, as shown in the figure. Then, use double-sided foam tape to attach the wireless data transmission module horizontally to the front end of the 3D printed board.




## 1.11 Parameter Configuration

To configure parameters, connect the flight controller to the computer using a USB cable and wait for the connection to complete in QGC software. Then, use one of the following methods:

1. Load the parameter list directly through QGC:
   - Click on the G icon in the upper left corner -> Vehicle Setup -> Parameters.
   - Click on Tools in the upper right corner -> Load Parameters.
   - Select `Mantis3.params` and the required parameters will be updated.
   - Restart the flight controller by unplugging and re-plugging the USB cable.
   - To ensure that the parameter modification is successful, wait for QGC to connect again (if it fails to connect, restart QGC or check if the USB cable is properly connected).
   - Click on the G icon in the upper left corner -> Vehicle Setup -> Parameters.
   - Search for MAV and check if `MAV_1_Config` is set to `GPS1`, `MAV_1_Mode` is set to Normal, `MAV_2_Config` is set to `TELEM1`, and `MAV_2_Mode` is set to Onboard.
   - If not, the parameter modification is incorrect and should be manually modified using Method 2.
   - Search for `MC_PITCHRATE_P` and check if it is set to 0.08.
   - If not, the parameter modification is incorrect and should be manually modified using Method 2.
   - After completing the above checks, disconnect the USB cable and power the flight controller using a battery. The wireless data transmission is now working, and the computer can search for WIFI: CUAVWLINK with the password `cuavwlink` to wirelessly connect to the flight controller.
2. Manually modify parameters:
   - To ensure that the wireless data transmission works properly, the parameters indicated in red in the figure below must be configured:
   - Connect the flight controller via USB (battery disconnected), open the QGC software, click the G icon in the upper left corner, go to Vehicle Setup, and then Parameters. Search for MAV.
   - Note that MAV_1_MODE and others will only appear if GPS1 is selected instead of Disable in `MAV_1_CONFIG`. Similarly, `MAV_2_MODE` will only appear if TELEM1 is selected instead of Disable in `MAV_2_CONFIG`. If `MAV_1_MODE` or `MAV_2_MODE` do not appear after selection, disconnect the USB cable, close QGC, reconnect, and search for the parameter again.
   - Once the configuration is completed, disconnect the USB cable and power the flight controller with a battery. The wireless data transmission should work now. Search for WIFI: CUAVWLINK xxxx on your computer, enter the password `cuavwlink`, and connect to the WIFI network. Then open the QGC software to wirelessly connect to the flight controller.





Next, you need to further modify the PID parameters of the flight controller. You can use either USB or wireless transmission to connect to QGC. Click the G icon in the upper left corner, go to Vehicle Setup, and select Parameters. Then, choose Multicopter Rate Control and Multicopter Attitude Control, and modify the relevant parameters as shown in the following figure (default parameters are white, and modified parameters are red).

## 1.12 Assembling the Drone Frame

Insert the board that was just installed from the bottom of the mainboard (as shown in the figure below), making sure that the motor wires are threaded out near the slot without being compressed, and the same is true for the wires of other components, which must not be compressed. Then use M2.6 x 8 self-tapping screws (with pointed ends) to connect the board to the mainboard, and install the four motors upside down on the motor base of the mainboard. The motor installation uses M2x6 ordinary hexagon screws (not self-tapping). The screw length provided with the motor box may not be suitable, so you need to choose M2x6 ordinary hexagon screws by yourself, and note that **the tip of the screw cannot touch the copper wire of the motor!**
Finally, use M2.6 x 12 self-tapping screws to connect the landing gear to the mainboard. The screws on the landing gear and mainboard are fitted with a shock-absorbing rubber sleeve, as shown in the figure on the far right. After installation, thread a hook and loop fastener through the gap between the two for attaching the battery. Do not install the propellers yet!

 
 

After the assembly is completed, it should look like the image below.

 

 


> Do not install the propellers at this point to avoid potential danger in the next step.

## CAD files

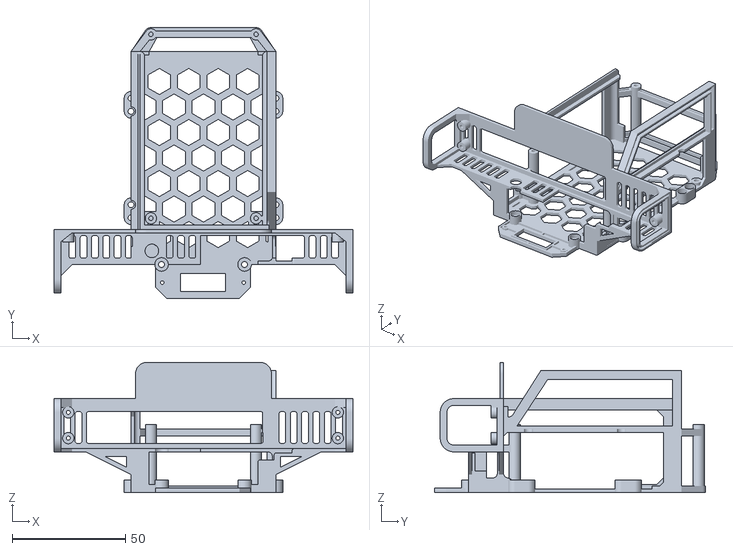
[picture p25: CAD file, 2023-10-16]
model/upper-for-seeedstudio.stl
132.0 x 119.6 x 57.5

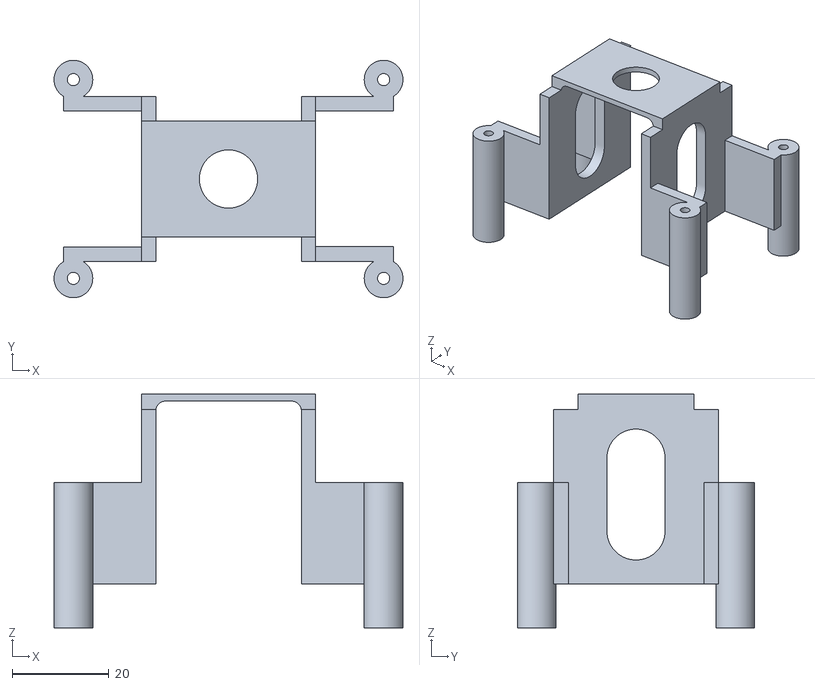
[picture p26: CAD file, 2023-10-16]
model/support.stl
72.0 x 49.0 x 48.2

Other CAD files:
model/main_board_with_guard.dwg
model/guard_bottom_separated.dwg
model/guard_bottom.dwg

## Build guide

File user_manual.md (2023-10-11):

# User Manual

## Password

- Onboard Computer
  Password: cor-drones
- WiFi Router
  - Name: COR-AMR
    Password: cor-drones
  - Name: AGoodWifi
    Password: Agoodpassword123

## WiFi Router

Name: COR-AMR
Password: cor-drones

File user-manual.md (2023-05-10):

# User Manual

## Onboard Computer

Password: cor-drones

## WiFi Router

Name: COR-AMR
Password: cor-drones

## ROS Multi-Machine Communication

1. Use `hostname` to query the hostname of your computer. E.g. you get `laptop` for your laptop and `drone1-desktop` for your drone.
2. Type `ifconfig` to query the IP address. E.g. you get `192.168.1.100` for your laptop and `192.168.1.101` for your drone.
3. Modify the `/etc/hosts` file on both machines (you will need sudo access), fill in the IP address and corresponding hostname.
4. Edit the `~/.bashrc` file on both machines, configure ROS_HOSTNAME and ROS_MASTER_URI variables as follows:
   ```
   export ROS_HOSTNAME=<hostname-of-this-machine>
   export ROS_MASTER_URI=http://<hostname-of-master-machine>:11311
   ```
   Note: The master machine is the machine where you start `roscore`. If you run `roscore` in the wrong machine, you will receive a warning when you start the `roscore`.
5. Remember to `source` the updated `~/.bashrc` file.
   Note: If there are some mistakes in the settings, you will receive an error message like this: _ROS_HOSTNAME / ROS_IP is set to only allow local connections, so a requested to `<some-machine>` is being rejected_. The ROS message from the remote machine may not be accepted to the master machine.

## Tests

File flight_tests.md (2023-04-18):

# Flight Tests

## 1.1 Pre-flight Test

1. Power the drone with the battery, but do not install the propellers.
2. Unlock the remote controller by moving the control sticks to the innermost position.
3. Gently push the throttle stick to spin up the motors.
4. Tilt the drone in different directions and verify if the motor speeds adjust appropriately. The motor closer to the ground should spin faster.
5. If the motor speed adjustment is not appropriate, recheck the parameter settings in step 1.7 and the levelness of the drone in step 1.8.

## 1.2 Sensor Recalibration

Connect the flight controller to a computer with QGC installed using a USB cable. Click on the G icon in the upper left corner, then select Vehicle Setup -> Sensor Calibration. Calibrate the Gyroscope, Accelerometer, and Level Horizon in sequence (for aircraft with an external magnetometer, also calibrate the magnetometer).

## 1.3 Installing Propellers

Take out a set of 4 propellers and first install the screw fixing seat in the center of each propeller. Note that propellers have a specific rotation direction. The thicker side is the leading edge, and the side with the pointed tip is the trailing edge. The image below shows that the propellers rotate in different directions on the left and right sides. The correct rotation direction is indicated by the arrow.

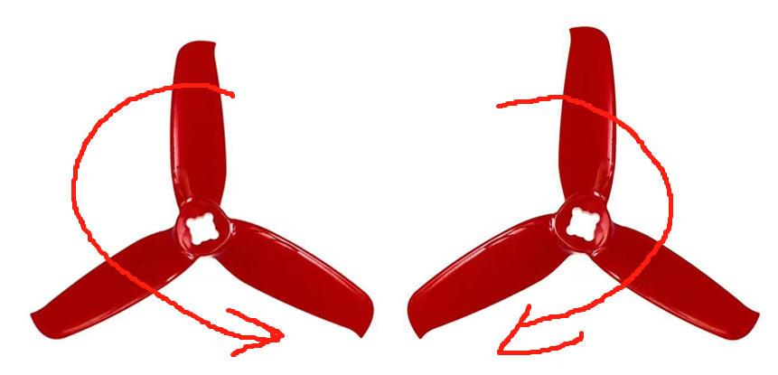
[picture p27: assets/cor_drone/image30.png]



## 1.4 Flight Test

Read the first flight guidelines: <https://docs.px4.io/main/en/flying/first_flight_guidelines.html>
Find an open area to test fly, and be sure to control the throttle precisely.
Experienced pilots can fly as they wish.
